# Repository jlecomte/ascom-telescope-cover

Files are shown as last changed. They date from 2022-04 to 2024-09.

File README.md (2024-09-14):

# ASCOM-Compatible Telescope Cover

I do not charge anything to create and maintain these open-source projects. But if you would like to say "thanks" for this project, feel free to send any amount through Paypal using the button below. I appreciate your support!

(https://www.paypal.com/donate/?hosted_button_id=49UXY8F6VVYFA)

:warning: **IMPORTANT:** :warning: This project is no longer actively maintained. Instead, check out [my new Telescope Cover V2](https://github.com/jlecomte/ascom-telescope-cover-v2).

<!-- toc -->

- [Introduction](#introduction)
- [Pre-Requisites](#pre-requisites)
- [Hardware](#hardware)
- [ASCOM Driver](#ascom-driver)
  - [Downloading And Installing The Driver](#downloading-and-installing-the-driver)
  - [Compiling The Driver (For Developers Only)](#compiling-the-driver-for-developers-only)
- [Arduino Firmware](#arduino-firmware)
  - [Microcontroller Compatibility](#microcontroller-compatibility)
  - [Compiling And Uploading The Firmware](#compiling-and-uploading-the-firmware)
- [Mechanical Components](#mechanical-components)
- [Electronic Circuit](#electronic-circuit)
- [Ideas For Future Improvements](#ideas-for-future-improvements)

<!-- tocstop -->

## Introduction

This repository contains code that allows you to build your own automated telescope cover. Here is a short demo video of the finished product, hosted on YouTube. Check it out!

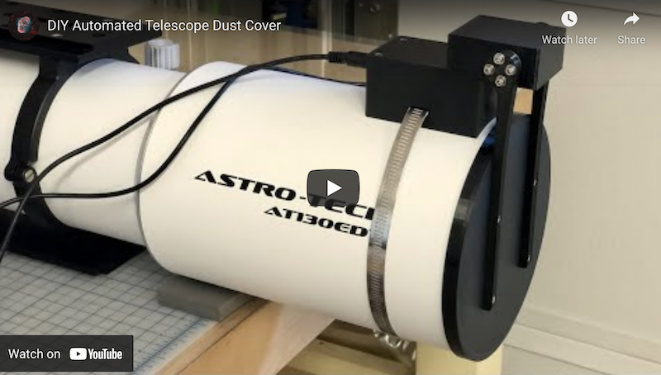
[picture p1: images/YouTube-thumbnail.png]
Short demo video of the finished product (https://www.youtube.com/watch?v=h6WpVCcGNUw)


In this repository, you will find:

* The code for the ASCOM driver (Microsoft Visual Studio 2022 project)
* The code for the Arduino firmware
* The various STL files to 3D print all the mechanical parts
* A blueprint for the electronic circuit

## Pre-Requisites

* A Windows computer (Windows 10 or newer)
* [Microsoft Visual Studio](https://visualstudio.microsoft.com/) (FYI, I used the 2022 edition...)
* [ASCOM Platform](https://ascom-standards.org/)
* [ASCOM Platform Developer Components](https://ascom-standards.org/COMDeveloper/Index.htm)
* [Arduino IDE](https://www.arduino.cc/en/software)
* [FreeCAD](https://www.freecadweb.org/), a free and open-source 3D parametric modeler
* A 3D printer able to print PETG, and a slicer (I use a heavily upgraded Creality Ender 3 v2, and Ultimaker Cura)
* A few basic tools that any tinkerer must own, such as a breadboard, a soldering iron, etc.

## Hardware

The following are just suggestions... Also, over time, some of the Amazon links may no longer work...

* [Seeeduino XIAO](https://www.seeedstudio.com/Seeeduino-XIAO-Arduino-Microcontroller-SAMD21-Cortex-M0+-p-4426.html) (You can get it quicker from Amazon, but you will have to pay twice as much!)
* [Mini360 Buck Converters](https://www.amazon.com/dp/B07T7L51ZW?tag=darkskygeek-20)
* [Perforated Circuit Board (PCB)](https://www.amazon.com/dp/B07NM68FXK?tag=darkskygeek-20)
* [DC Power Jack](https://www.amazon.com/dp/B01N8VV78D?tag=darkskygeek-20)
* [High torque quality Servo with 270° control angle](https://www.amazon.com/dp/B07S9XZYN2?tag=darkskygeek-20)
* [Aluminum Servo Horn](https://www.amazon.com/dp/B07D56FVK5?tag=darkskygeek-20)
* [Bench Power Supply](https://www.amazon.com/dp/B07GCJ5QHF?tag=darkskygeek-20)
* [Threaded inserts for 3D printed parts](https://www.amazon.com/dp/B07VFZWWXY?tag=darkskygeek-20)
* [Assortment of small metric screws, nuts, and washers](https://www.amazon.com/dp/B08JCKH31Q?tag=darkskygeek-20)
* [22AWG solid core electrical wires](https://www.amazon.com/dp/B088KQFHV7?tag=darkskygeek-20)
* [Easy-to-print PETG filament](https://www.amazon.com/dp/B07PGYHYV8?tag=darkskygeek-20)
* [Stainless steel cut-to-length hose clamp](https://www.amazon.com/dp/product/B08Y6LSL3R?tag=darkskygeek-20)

## ASCOM Driver

### Downloading And Installing The Driver

**Step 1:** Download the driver from the [releases page](https://github.com/jlecomte/ascom-telescope-cover/releases), and place the file `ASCOM.DarkSkyGeek.TelescopeCover.dll` somewhere on your system (example: `C:\Users\julien\ascom-telescope-cover\`).

**Step 2:** Open a command prompt, but make sure you run it **as an administrator**!

**Step 3:** Then, proceed with the installation of the driver using `RegAsm.exe`, a utility that should already be present on your system (it comes with the .NET framework). Just don't forget to use the 64 bit version, and to pass the `/tlb /codebase` flags. Here is what it looked like on my imaging mini computer:

```
> cd C:\Users\julien\ascom-telescope-cover\
> C:\Windows\Microsoft.NET\Framework64\v4.0.30319\RegAsm.exe /tlb /codebase ASCOM.DarkSkyGeek.TelescopeCover.dll
Microsoft .NET Framework Assembly Registration Utility version 4.8.4161.0
for Microsoft .NET Framework version 4.8.4161.0
Copyright (C) Microsoft Corporation.  All rights reserved.

Types registered successfully
```

**Note:** The output may be more verbose than the above. As long as it says `Types registered successfully`, you are good to go!

**Note:** During registration, you will see a warning that the assembly is unsigned. This is normal as I did not bother going through the pain of signing the assembly, so you will just have to trust that you are registering the DLL that I built and uploaded to GitHub. And if you don't trust me / GitHub, you can build the DLL yourself using Visual Studio.

**Note:** Once the driver has been installed, make sure you do _not_ delete or move the `ASCOM.DarkSkyGeek.TelescopeCover.dll` file, or things will not work! (if you do move it, you will need to register it again in its new location)

**Step 4:** Start (or restart, if it was already running) N.I.N.A. (or whatever application you use to control your equipment).

### Compiling The Driver (For Developers Only)

Open Microsoft Visual Studio as an administrator (right click on the Microsoft Visual Studio shortcut, and select "Run as administrator") This is required because when building the code, by default, Microsoft Visual Studio will register the necessary COM components, and this operation requires special privileges (Note: This is something you can disable in the project settings...) Then, open the solution (`ASCOM_Driver\ASCOM.DarkSkyGeek.TelescopeCover.sln`), change the solution configuration to `Release` (in the toolbar), open the `Build` menu and click on `Build Solution`. As long as you have properly installed all the required dependencies, the build should succeed and the ASCOM driver will be registered on your system. The binary file generated will be `ASCOM_Driver\bin\Release\ASCOM.DarkSkyGeek.TelescopeCover.dll`. You may also download this file from the [Releases page](https://github.com/jlecomte/ascom-telescope-cover/releases).

## Arduino Firmware

### Microcontroller Compatibility

Pretty much all Arduino-compatible boards should work. There is nothing magical about the firmware. However, see the comment regarding the pins and the servo library. Depending on the exact board you picked, you might have to change that.

### Compiling And Uploading The Firmware

* Add support for Seeeduino boards by following [the instructions from the board manufacturer](https://wiki.seeedstudio.com/Seeeduino-XIAO/).
* To customize the name of the device when connected to your computer, open the file `boards.txt`, which, on my system and for the version of the Seeeduino board I am using, is located at `%LOCALAPPDATA%\Arduino15\packages\Seeeduino\hardware\samd\1.8.2\boards.txt`. Then, change the value of the key `seeed_XIAO_m0.build.usb_product` from `Seeed XIAO M0` (default) to whatever you'd like.
* Finally, connect your Seeeduino board to your computer (make sure you use a USB-C cable that supports data and not just power!), open the sketch file located at `Arduino_Firmware\Arduino_Firmware.ino`, and click on the `Upload` button in the toolbar.

## Mechanical Components

Here is a 3D rendering of all the parts involved in this project:

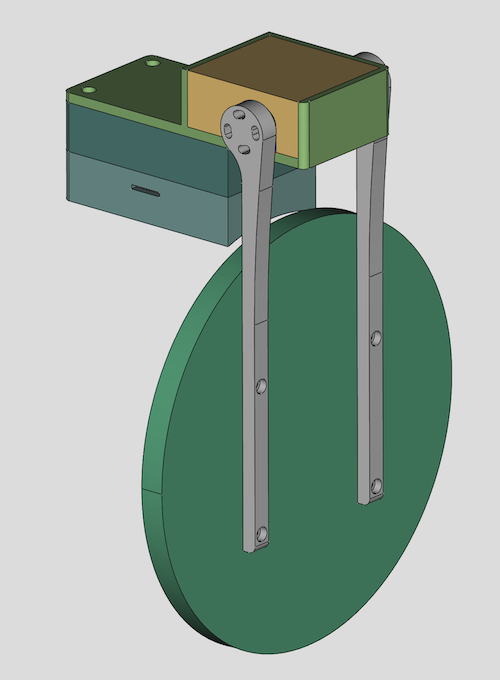
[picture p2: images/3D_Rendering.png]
3D Rendering


The STL files you will find in the `3D_Files/` folder are just a starting point. You will likely have to create your own version of this project, if only to match the base curvature to your own OTA... That is why I included the FreeCAD file in this repository! (also in the `3D_Files/` folder)

## Electronic Circuit

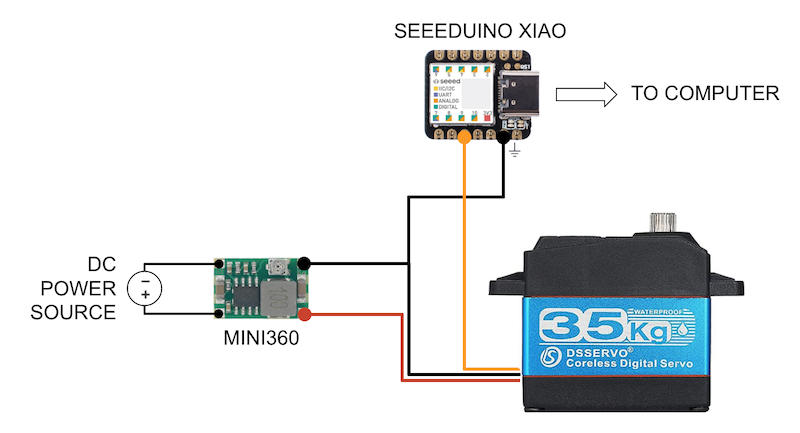
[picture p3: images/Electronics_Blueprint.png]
Electronics Blueprint


Here is what the electronic circuit looks like:

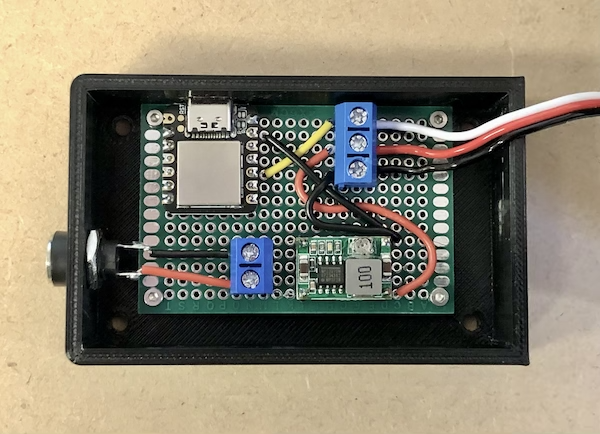
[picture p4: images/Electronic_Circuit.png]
Electronic Circuit


In the photograph above, the components were soldered onto a 60mm x 40mm PCB.

## Ideas For Future Improvements

* Remove the need for a separate 12V power connector, i.e. use the USB cable for both data and power. This change would prevent us from using an Arduino-compatible board because the maximum current that can be delivered by an Arduino-compatible board is usually around 200mA, which is not enough for a powerful servo. In order to do this, you'd have to basically build your own Arduino board using a micro-controller, a USB jack, a USB driver, and many other components... It's quite a project on its own, which is why I decided to go the "easy" route... Alternatively, I found a unit called "PD Micro" which implements USB-C power delivery. I have not tried it yet, but it looks promising.
* Automatically sense the position of the cover before powering up the servo. Right now, if you power up the unit while the cover is open, it will suddenly close very quickly. That can be quite a jarring experience the first time you see it happen. And if something is in the way (example: a flat panel), you could potentially damage your equipment. This could be solved with a simple potentiometer attached to the servo arm.
* Integrate a flat field panel inside the cover. I wanted to keep this project relatively simple, and I did not want to add any more weight to the front end of my already front heavy refractor, so I skipped that, but it can be done and would be a great addition to this project!

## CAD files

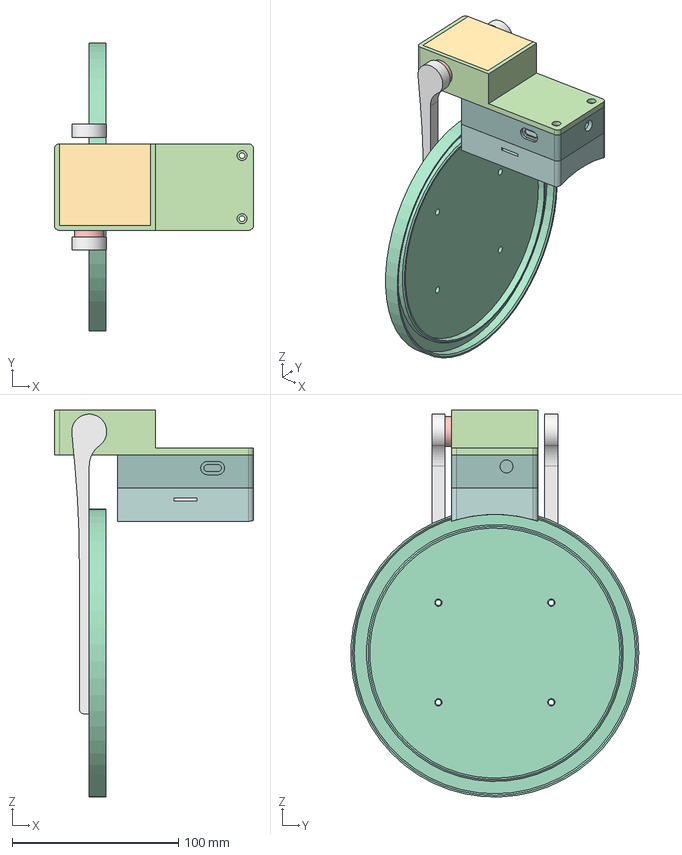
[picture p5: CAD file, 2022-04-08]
3D_Files/Automated-Telescope-Dust-Cover.FCStd
120.0 x 173.2 x 233.0 mm
Circuit Board Box
Base Body
Servo Holder
Servo Lid
Bushing
Cover
Left Cover Arm
Right Cover Arm

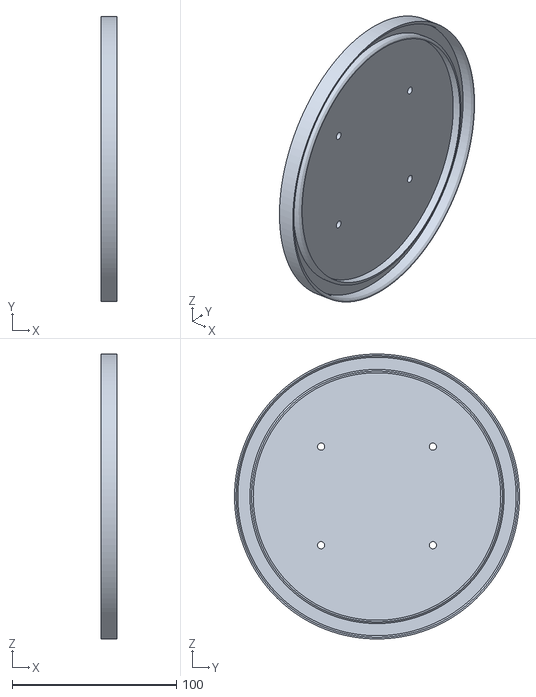
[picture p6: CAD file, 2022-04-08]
3D_Files/Cover.stl
10.0 x 173.4 x 173.3

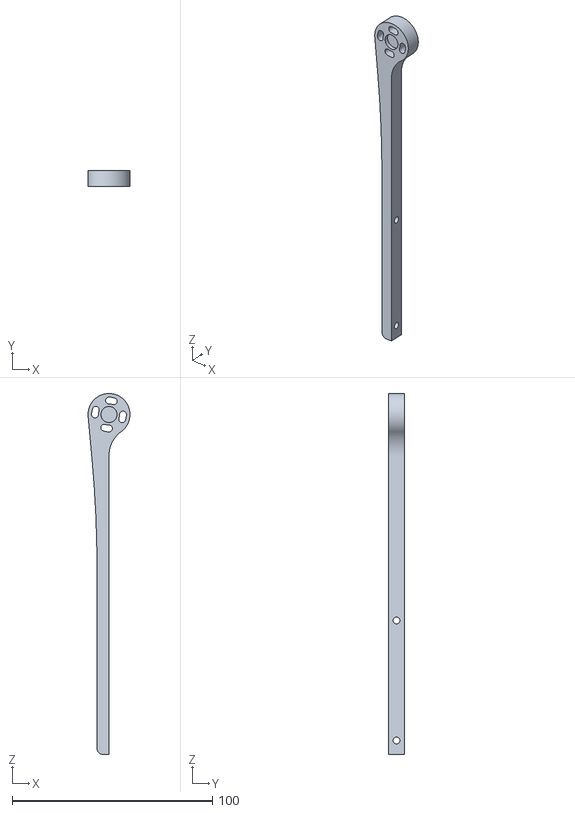
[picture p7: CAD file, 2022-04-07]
3D_Files/Right_Cover_Arm.stl
21.0 x 8.00 x 180.5

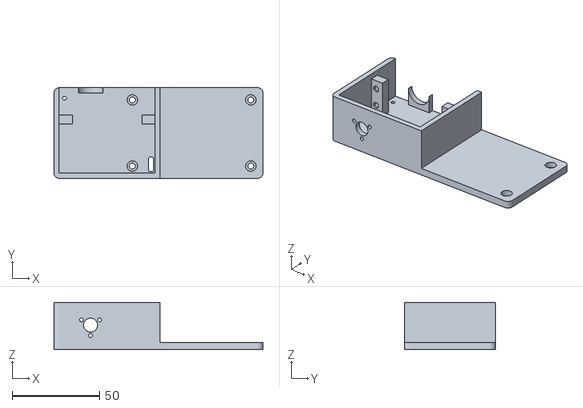
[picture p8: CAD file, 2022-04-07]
3D_Files/Servo_Holder.stl
120.0 x 52.0 x 27.0

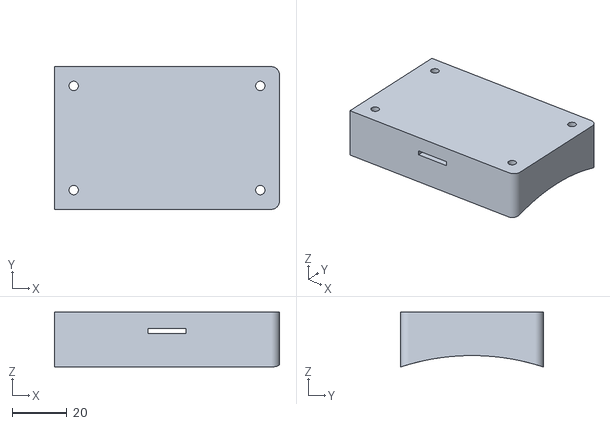
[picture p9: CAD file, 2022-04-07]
3D_Files/Base.stl
82.0 x 52.0 x 20.0

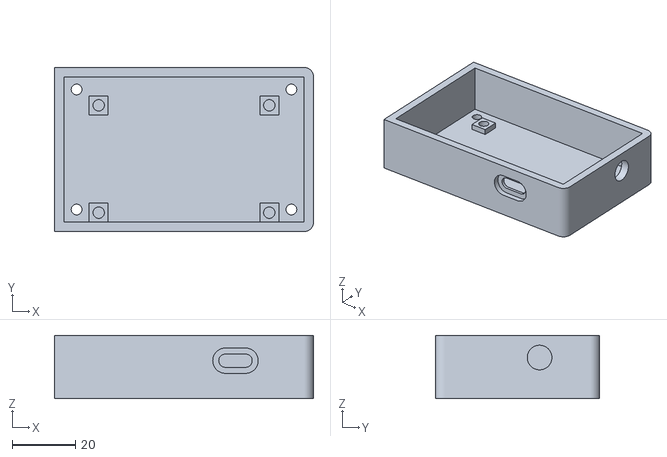
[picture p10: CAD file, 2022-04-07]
3D_Files/Circuit_Board_Box.stl
82.0 x 52.0 x 20.0

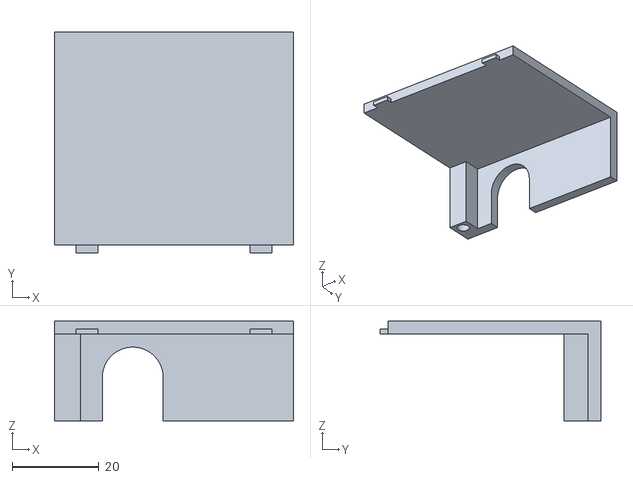
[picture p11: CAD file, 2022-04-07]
3D_Files/Servo_Lid.stl
55.0 x 50.8 x 23.0

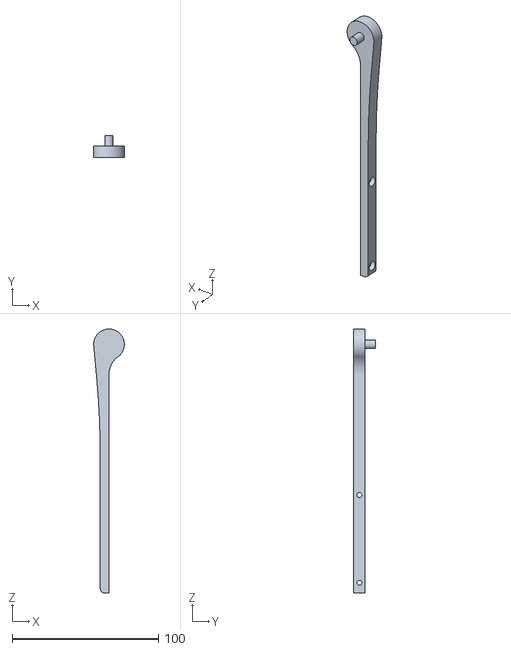
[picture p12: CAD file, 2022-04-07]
3D_Files/Left_Cover_Arm.stl
21.0 x 15.0 x 180.5

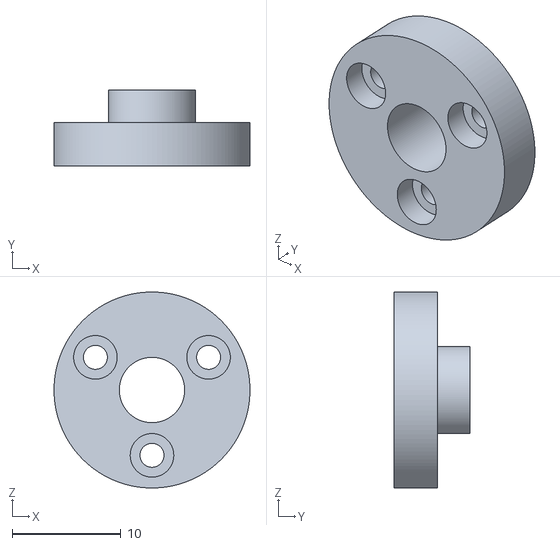
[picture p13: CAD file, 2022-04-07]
3D_Files/Bushing.stl
18.0 x 7.00 x 18.0

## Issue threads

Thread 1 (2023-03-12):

Merge some of your projects

JeffStor, 2023-03-12:
Hello Julien,

No issue, no pull request, just a thought. My name is Jean-Francois, I live in France, and I am a (low level) astrophotographer.
I use NINA and Ascom devices. My setup is EQ6-R / Askar FRA600 /ASI2600color.

I was seeking for an automated dust cap for my telescope and I found your videos ! (Dark Sky Geek)
You did such a great job for 2 projects in which I am interested : dust cap and focuser.
I am not a developer and I discovered your channel today !
I bought hardware stepper-motors drivers called TIC from Pololu and I did a small GUI to drive manually stepper-motors.
This was easy, but to integate TIC with NINA (native or Ascom) is much to dffificult for me.

A stepper-motor and a stepper motor is much less expensive that any Zwo, Pegasus or else equipment.

If for any reason, you plan to use Pololu TIC hardware to drive stepper-motors for your new projects, please let me know.

Sincerely

Jean-Francois
jf.eble@laposte.net

jlecomte, 2023-03-12:
Thank you for your interest. I do not plan to use "Pololu TIC" hardware (I have never heard of that brand before). I generally stick to dirt cheap, standard stepper motors or servos that you can find anywhere online. That being said, adapting what I've done to your specific hardware shouldn't be too difficult. Best of luck!

JeffStor, 2023-03-12:
Thank you for your quick answer. By the way I choosed TIC + stepper-motors because I can buy both on Amazon for around  50 euros (plus a 3D printed hardware for virtually nothing) when a focuser from ZWO or Pegasus costs more than  250 euros

Clear skies !

Closed 2023-03-12.

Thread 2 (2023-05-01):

Issue with FreeCAD model

rlavriv, 2023-05-01:
When I am trying to change globals in FreeCAD model to adjust to my OTA, I get issue with model recompile.

The issue seem to be with USB Connector hole sketch, which shows in a wrong plane:
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

Any ideas how to fix it?

jlecomte, 2023-05-01:
That is because of the topological naming problem, which is a huge issue in FreeCAD. See:

* https://wiki.freecad.org/Topological_naming_problem
*  https://ondsel.com/blog/freecad-topological-naming/

Unfortunately, I did not follow the best practices when designing this model, and therefore it is a victim of this issue.

Since I may upgrade my scope to a larger one, I may completely redesign this in FreeCAD, but this time doing it correctly (and also simplifying the design a bit)...

rlavriv, 2023-05-01:
Is there absolutely no way to salvage it?

jlecomte, 2024-05-25:
I don't think so. Now, I'm hearing that FreeCAD 0.22 will have mostly solved the topological naming issue, so it might be worth trying then. best of luck!

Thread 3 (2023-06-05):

WriteProfile autoDetectComPort alway be true

ZetChang, 2023-06-05:
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

jlecomte, 2023-06-05:
Good catch, thanks!

jlecomte, 2023-06-05:
Fixed in https://github.com/jlecomte/ascom-telescope-cover/commit/37df01e01ec9c3148f8a7f52a69194fa1b1d81bb and release v1.0.1.

ppurbano, 2024-04-14:
Hello. I love their projects and I have made both the flats generator and the telescope cover. I would like to ask you if it would be possible to join the two circuits into a single XIA0. It would be greatly appreciated. A strong greeting

Closed 2023-06-05.

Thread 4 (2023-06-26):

2 servos instead of one ?

aras-vbo, 2023-06-26:
Hello Julien,

Vincent from France. Many thanks for your project ! I'm currently making a cover for my remote telescope.
This is just an idea. Is it possible to control 2 servos from the Xiao at the same time instead of one ? My telescope has a diameter of 250 mm and I'm not able to make a dust cap in just one piece. I need to use 2 parts in shapes of half-circle.
Do you think it could be difficult to add this feature, by changing the Xiao firmware only ?

I think I will try for fun !

Vincent

Closed 2023-06-26.

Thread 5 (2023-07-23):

Not working in NINA

Antiath, 2023-07-23:
NINA doesn't work with your ASCOM driver.  It can connect and open the cover fine. But after asking NINA to open the cover, it times out, preventing me from closing the cover.

I ran the driver along with NINA in Visual Studio to investigate this and I think I know what happens. When lauching the driver, NINA has the switch defaulted to Off and the cover is closed by default of course. All is well for now.  When activating the switch to open the cover, it does so and NINA starts polling the GetSwitchValue method and it expects it to return a 1 when the switch is ON ( i.e cover open). Your driver outputs the opposite. It happens here :

```
     public double GetSwitchValue(short id)
        {
            Validate("GetSwitchValue", id);
            tl.LogMessage("GetSwitchValue", $"GetSwitchValue({id}) - not implemented");
            return QueryDeviceState() ? 1.0 : 0.0;
        }
```
So the solution is simple :
`return QueryDeviceState() ? 0.0 : 1.0;`
and also
` internal static string traceStateDefault = "true"; `

Maybe  a switch driver is not the best option for this application.
Personnaly I would have used a Flatplanel template for the driver, instead of a switch. Even if you don't have an actual flat panel in the cover,  the template provides the methods for the motorised part. So you can just leave the flat side in the code and just implement the motor part.
Also I already have a power box occupying the switch part of NINA, so it's not helpful to have to change driver just to move the cover.

jlecomte, 2023-07-23:
@Antiath I have been using my driver and my device in NINA for well over a year (totaling about 50 nights) and it has worked very reliably.

`QueryDeviceState()` returns `true` if the cover is open, and `false` otherwise, which means that `GetSwitchValue()` will return `1.0` if the cover is open, and `0.0` otherwise. That is the expected behavior.

Antiath, 2023-07-23:
Ah yes my bad, ths issue was with the firmware. I had to modify it a bit to accomodate my servomotor who was weirdly turning the opposite way. And I forgot to check change the state variable accordingly to match this. That is corrected and working as expected now. Case closed.

Nevertheless I will probably reuse the code for and port it to a different driver

Closed 2023-07-23.

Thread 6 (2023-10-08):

Thanks for this project

astroalex80, 2023-10-08:
Dear Julien,

Thanks for making the cover as well as flat panel available.

Converted the cad files to Fusion360 to make them fit my scope. Combined both flat panel and cover functionality.

Honesty my mistake of not having used an SAMD21 / Seeeduino XIAO before. What a powerful tiny piece of electronics.

Instead the usual servo lib I'm using one called slowServo allowing good control of the speed and it is working asynchronously and not blocking when servo moves. It therewith better follows the ASCOM specs like reporting status when moving.

The fact of fast closure move on power-up when cover is not closed I could overcome by writing either panel open, closed or moving to the Flash memory of the XIAO. Therewith current cover status remains on power up, unless the XIAO is disconnected while servo is moving. In this case the cover opens on the re-connection, as feels more save to me before moving fast into the dew shield.

3d parts are printed, cover is moving but wiring is still on a breadboard. Will assemble it next days and happily share some pictures.

Kind regards from Germany,
Alex

jlecomte, 2023-10-09:
Thanks for the kind words, Alex! These are really good suggestions, and I will incorporate some of them into the version 2 of this project, next year. Among other things, I want the cover to know which state it is in when powered up, and this can be accomplished using a potentiometer and a bit of logic in the software. Tschüss!

astroalex80, 2023-10-10:
By the way regarding reading the cover position. I havent been aware they exist but just ordered two of these:
Feetech FB5118M Digital Servo 7.4V 17kg.cm with Position Feedback

There is a 4. wire linked to the internal potentiometer of the servo and therewith having the build-in capability of providing postion.

jlecomte, 2023-10-10:
I did not know that some servos had position feedback. I just ordered one on Amazon, I’ll be experimenting with it. If it works, this would be a brilliant solution! Thanks a lot :)

Closed 2023-10-09.

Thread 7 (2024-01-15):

Control two covers from one computer?

OregonAstronomer, 2024-01-15:
Hi,
First, I'd like to thank you for this great project. It has been working flawlessly in my remote observatory for the past year!
I'm planning on adding a second camera with an attached telephoto lens piggyback on top of the scope I am currently using and would like to also equip it with one of your covers. Is it possible to control two covers using two instances of NINA from a single computer?
Thank you so much for your time.
Sincerely,
Arnie (OregonAstronomer)

Adler6907, 2024-01-15:
I programmed an extension for exactly this.

https://github.com/Adler6907/ascom-telescope-cover/tree/Adler6907-multiple-Telescope-Cover

jlecomte, 2024-01-15:
Yes, it is possible to control two covers using two instances of NINA on a single computer.

OregonAstronomer, 2024-01-16:
Thank you both so much!

Closed 2024-01-15.

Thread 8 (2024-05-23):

Added control (third state) to turn on flatpanel (and added COMMAND:FLAT in ARDUINO project), but...

thegoodpope, 2024-05-23:
...but i cannot regasm the assembly.

My Visual Studio 2019 refuses to install as COM the resulting dll.
"RA0000 .... is not a valid assembly."
I'm a programmer but not expert with C# and Visual studio in general. Is there something I've to change in order to compile and install the driver?
I ask to you because:
1) I cannot find real and useful explanations. I've attempted to put signature, change GUID and a lot of other things
2) I cannot install - also - the compiled result of your original code
3) nevertheless the installation of your COM dll component (very useful your HUB also! Thank you) runs perfectly...so are there differences between the COM component you distribute and the project you share?

Thanks in every case for your project. I've customized the original cap/legs/base for my scope (a 20cm newton) and all went well.

jlecomte, 2024-05-24:
> Is there something I've to change in order to compile and install the driver?

No. It should work out of the box. This, however, assumes that you already have the ASCOM platform installed on your development computer.

Closed 2024-05-24.

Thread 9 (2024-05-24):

Cannot connect properly in NINA

sidiouss, 2024-05-24:
Hello,
I've successfully prepared slightly modified flat panel and telescope cover projects which I am very thankful for. I managed to register both drivers and setup properly the flat panel in Nina. However, I cannot launch the cover in the Nina software. It says both that the switch is connected, but then also prompts that there is invalid response from the cover. Can you help me investigating this issue?
The cover properly shows up in the device manager as a com port, I can send the commands through the COM terminal so I know the cover works, but I cannot launch it with NINA. I am using the newest dll and firmware is uploaded to Arduino Nano.

Prompt from NINA:
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

jlecomte, 2024-05-24:
I do not know what is causing this, and I cannot provide you with any support.

sidiouss, 2024-05-25:
Hi,
You may not be eager to solve such problems and I understand that. However, I have run conformance checker on your driver and as you are more familiar with ASCOM platform, maybe you could identify the underlying issue presented in the following report:

ConformanceCheck ASCOM Device Conformance Checker Version 6.6.8048.17861, Build time: 2022-01-13 08:55:24
ConformanceCheck Running on: ASCOM Platform 6.6 SP2 6.6.2.4294

ConformanceCheck Driver ProgID: ASCOM.DarkSkyGeek.Switch

Error handling
Error number for "Not Implemented" is: 80040400
Error number for "Invalid Value 1" is: 80040405
Error number for "Value Not Set 1" is: 80040402
Error number for "Value Not Set 2" is: 80040403
Error messages will not be interpreted to infer state.

21:45:03.873 Driver Access Checks              OK
21:45:04.535 AccessChecks                      OK       Successfully created driver using late binding
21:45:06.583 AccessChecks                      OK       Successfully connected using late binding
21:45:06.588 AccessChecks                      INFO     The driver is a .NET object
21:45:06.593 AccessChecks                      INFO     The AssemblyQualifiedName is: ASCOM.DarkSkyGeek.Switch, ASCOM.DarkSkyGeek.TelescopeCover, Version=1.0.0.0,
21:45:06.599 AccessChecks                      INFO     The driver implements interface: ASCOM.DeviceInterface.ISwitchV2
21:45:07.277 AccessChecks                      INFO     Device does not expose interface ISwitch
21:45:09.339 AccessChecks                      INFO     Device exposes interface ISwitchV2
21:45:10.014 AccessChecks                      OK       Successfully created driver using driver access toolkit
21:45:12.063 AccessChecks                      OK       Successfully connected using driver access toolkit

Conform is using ASCOM.DriverAccess.Switch to get a Switch object
21:45:12.099 ConformanceCheck                  OK       Driver instance created successfully
21:45:14.211 ConformanceCheck                  OK       Connected OK

Common Driver Methods
21:45:14.265 InterfaceVersion                  OK       2
21:45:14.305 Connected                         OK       True
21:45:14.352 Description                       OK       DarkSkyGeek’s Telescope Cover
21:45:14.398 DriverInfo                        OK       DarkSkyGeek’s Telescope Cover ASCOM Driver Version 1.0
21:45:14.445 DriverVersion                     OK       1.0
21:45:14.492 Name                              OK       DarkSkyGeek’s Telescope Cover
21:45:14.538 CommandString                     INFO     Conform cannot test the CommandString method
21:45:14.547 CommandBlind                      INFO     Conform cannot test the CommandBlind method
21:45:14.557 CommandBool                       INFO     Conform cannot test the CommandBool method
21:45:14.565 Action                            INFO     Conform cannot test the Action method
21:45:14.574 SupportedActions                  OK       Driver returned an empty action list

Properties
21:45:14.734 MaxSwitch                         OK       1

Methods
21:45:15.001 SwitchNumber                      ISSUE    Received ASCOM.DriverException(0x80040401), please use ASCOM.InvalidValueException to report invalid values
21:45:15.009 SwitchNumber                      ERROR    Unexpected DriverException(0x80040401), when a switch ID below 0 was used in method: CanWrite: CanWrite set - '-1' is an invalid value. The valid range is: 0 to 0.
21:45:15.019 SwitchNumber                      ISSUE    Received ASCOM.DriverException(0x80040401), please use ASCOM.InvalidValueException to report invalid values
21:45:15.027 SwitchNumber                      ERROR    Unexpected DriverException(0x80040401), when a switch ID above MaxSwitch was used in method: CanWrite: CanWrite set - '2' is an invalid value. The valid range is: 0 to 0.
21:45:15.037 SwitchNumber                      ISSUE    Received ASCOM.DriverException(0x80040401), please use ASCOM.InvalidValueException to report invalid values
21:45:15.045 SwitchNumber                      ERROR    Unexpected DriverException(0x80040401), when a switch ID below 0 was used in method: GetSwitch: GetSwitch set - '-1' is an invalid value. The valid range is: 0 to 0.
21:45:15.055 SwitchNumber                      ISSUE    Received ASCOM.DriverException(0x80040401), please use ASCOM.InvalidValueException to report invalid values
21:45:15.063 SwitchNumber                      ERROR    Unexpected DriverException(0x80040401), when a switch ID above MaxSwitch was used in method: GetSwitch: GetSwitch set - '2' is an invalid value. The valid range is: 0 to 0.
21:45:15.075 SwitchNumber                      ISSUE    Received ASCOM.DriverException(0x80040401), please use ASCOM.InvalidValueException to report invalid values
21:45:15.085 SwitchNumber                      ERROR    Unexpected DriverException(0x80040401), when a switch ID below 0 was used in method: GetSwitchDescription: GetSwitchDescription set - '-1' is an invalid value. The valid range is: 0 to 0.
21:45:15.095 SwitchNumber                      ISSUE    Received ASCOM.DriverException(0x80040401), please use ASCOM.InvalidValueException to report invalid values
21:45:15.106 SwitchNumber                      ERROR    Unexpected DriverException(0x80040401), when a switch ID above MaxSwitch was used in method: GetSwitchDescription: GetSwitchDescription set - '2' is an invalid value. The valid range is: 0 to 0.
21:45:15.119 SwitchNumber                      ISSUE    Received ASCOM.DriverException(0x80040401), please use ASCOM.InvalidValueException to report invalid values
21:45:15.126 SwitchNumber                      ERROR    Unexpected DriverException(0x80040401), when a switch ID below 0 was used in method: GetSwitchName: GetSwitchName set - '-1' is an invalid value. The valid range is: 0 to 0.
21:45:15.138 SwitchNumber                      ISSUE    Received ASCOM.DriverException(0x80040401), please use ASCOM.InvalidValueException to report invalid values
21:45:15.147 SwitchNumber                      ERROR    Unexpected DriverException(0x80040401), when a switch ID above MaxSwitch was used in method: GetSwitchName: GetSwitchName set - '2' is an invalid value. The valid range is: 0 to 0.
21:45:15.158 SwitchNumber                      ISSUE    Received ASCOM.DriverException(0x80040401), please use ASCOM.InvalidValueException to report invalid values
21:45:15.168 SwitchNumber                      ERROR    Unexpected DriverException(0x80040401), when a switch ID below 0 was used in method: GetSwitchValue: GetSwitchValue set - '-1' is an invalid value. The valid range is: 0 to 0.
21:45:15.178 SwitchNumber                      ISSUE    Received ASCOM.DriverException(0x80040401), please use ASCOM.InvalidValueException to report invalid values
21:45:15.188 SwitchNumber                      ERROR    Unexpected DriverException(0x80040401), when a switch ID above MaxSwitch was used in method: GetSwitchValue: GetSwitchValue set - '2' is an invalid value. The valid range is: 0 to 0.
21:45:15.200 SwitchNumber                      ISSUE    Received ASCOM.DriverException(0x80040401), please use ASCOM.InvalidValueException to report invalid values
21:45:15.209 SwitchNumber                      ERROR    Unexpected DriverException(0x80040401), when a switch ID below 0 was used in method: MaxSwitchValue: MaxSwitchValue set - '-1' is an invalid value. The valid range is: 0 to 0.
21:45:15.221 SwitchNumber                      ISSUE    Received ASCOM.DriverException(0x80040401), please use ASCOM.InvalidValueException to report invalid values
21:45:15.229 SwitchNumber                      ERROR    Unexpected DriverException(0x80040401), when a switch ID above MaxSwitch was used in method: MaxSwitchValue: MaxSwitchValue set - '2' is an invalid value. The valid range is: 0 to 0.
21:45:15.241 SwitchNumber                      ISSUE    Received ASCOM.DriverException(0x80040401), please use ASCOM.InvalidValueException to report invalid values
21:45:15.258 SwitchNumber                      ERROR    Unexpected DriverException(0x80040401), when a switch ID below 0 was used in method: MinSwitchValue: MinSwitchValue set - '-1' is an invalid value. The valid range is: 0 to 0.
21:45:15.270 SwitchNumber                      ISSUE    Received ASCOM.DriverException(0x80040401), please use ASCOM.InvalidValueException to report invalid values
21:45:15.281 SwitchNumber                      ERROR    Unexpected DriverException(0x80040401), when a switch ID above MaxSwitch was used in method: MinSwitchValue: MinSwitchValue set - '2' is an invalid value. The valid range is: 0 to 0.
21:45:15.294 SwitchNumber                      ISSUE    Received ASCOM.DriverException(0x80040401), please use ASCOM.InvalidValueException to report invalid values
21:45:15.305 SwitchNumber                      ERROR    Unexpected DriverException(0x80040401), when a switch ID below 0 was used in method: SetSwitch: SetSwitch set - '-1' is an invalid value. The valid range is: 0 to 0.
21:45:15.320 SwitchNumber                      ISSUE    Received ASCOM.DriverException(0x80040401), please use ASCOM.InvalidValueException to report invalid values
21:45:15.330 SwitchNumber                      ERROR    Unexpected DriverException(0x80040401), when a switch ID above MaxSwitch was used in method: SetSwitch: SetSwitchValue set - '2' is an invalid value. The valid range is: 0 to 0.
21:45:15.343 SwitchNumber                      ISSUE    Received ASCOM.DriverException(0x80040401), please use ASCOM.InvalidValueException to report invalid values
21:45:15.356 SwitchNumber                      ERROR    Unexpected DriverException(0x80040401), when a switch ID below 0 was used in method: SetSwitchValue: SetSwitchValue set - '-1' is an invalid value. The valid range is: 0 to 0.
21:45:15.369 SwitchNumber                      ISSUE    Received ASCOM.DriverException(0x80040401), please use ASCOM.InvalidValueException to report invalid values
21:45:15.379 SwitchNumber                      ERROR    Unexpected DriverException(0x80040401), when a switch ID above MaxSwitch was used in method: SetSwitchValue: SetSwitchValue set - '2' is an invalid value. The valid range is: 0 to 0.
21:45:15.394 SwitchNumber                      ISSUE    Received ASCOM.DriverException(0x80040401), please use ASCOM.InvalidValueException to report invalid values
21:45:15.406 SwitchNumber                      ERROR    Unexpected DriverException(0x80040401), when a switch ID below 0 was used in method: SwitchStep: SwitchStep set - '-1' is an invalid value. The valid range is: 0 to 0.
21:45:15.419 SwitchNumber                      ISSUE    Received ASCOM.DriverException(0x80040401), please use ASCOM.InvalidValueException to report invalid values
21:45:15.430 SwitchNumber                      ERROR    Unexpected DriverException(0x80040401), when a switch ID above MaxSwitch was used in method: SwitchStep: SwitchStep set - '2' is an invalid value. The valid range is: 0 to 0.
21:45:18.735 GetSwitchName                     OK       Found switch 0
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

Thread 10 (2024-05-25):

Problems in WIN11 64bit

thegoodpope, 2024-05-25:
This terrific complexity with Window versions, 32/64 bit, ASCOM versions, .NET frameworks will kill me...
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

thegoodpope, 2024-05-25:
Registering in 32 bit ascom is ok, but when I tyy to connect in NINA
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

jlecomte, 2024-05-25:
I have had no such problem. I'm not sure what you're doing, but the Visual Studio project should be configured properly out of the box. When I last published the DLL, I simply opened the project, built it, and copied the DLL.

thegoodpope, 2024-05-26:
I've done the same, but got problems with regasm as i've alteady written.
This last thing has not to do with recompilation: I used your original
compiled DLL as downloaded from the resources sectiin. In my old PC It
worked flawlessy, buy when i've tried to install It on the win11 PC that
controls mount and camera (remotely) It has occurred the strange
situation....

Il dom 26 mag 2024, 01:51 Julien Lecomte ***@***.***> ha
scritto:

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

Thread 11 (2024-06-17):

Adjusting servo end courses and speed (delay)

vef445, 2024-06-17:
Hi,
First of all, be aware that I'm in no way a professional developer :)

With the driver you built, I wasn't able to get the full course of my 270deg. servo. A quick investigation revealed that the default values provided by Servo.h when attaching the servo (min pulse width = 544 and max pulse width = 2400) were not ideal for my setup. (Using the cheap servos from Amazon that you listed).

Instead of just editing the Arduino code with alternative (and fixed) values, I decided to add 'pulse min' and 'pulse max' as part of the Ascom driver profile.
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
While I was there, I also added the servo write "delay" as a parameter too. (the default value 30 isn't the best for my setup).

The three parameters are sent to the Arduino upon connection of the device in Nina. Please check how it's parsed on the Arduino side; it's a little dirty... (but it works :) )

I have no idea how I can properly share my code with you or if you're even interested. I'm simply attaching a ZIP below that contains both the driver and the Arduino file. Let me know if there is a better method.
[Motorized_cover_guillaume.zip](https://github.com/user-attachments/files/15865544/Motorized_cover_guillaume.zip)

Comments/critics very welcome!

-Guillaume

PS: Awesome job you did there! I already built two motorized covers, including one for my C11 and, despite the large size, it works perfectly.

jlecomte, 2024-06-17:
Hello! Great work! Note that this project is now on life support so I will not make any changes to it. However, I have been working on a new version of this project, which brings a lot of improvements, and fixes the servo pulse min/max thing you mentioned. I do not have an ETA to release that project. Thanks!

vef445, 2024-06-17:
> Hello! Great work! Note that this project is now on life support so I will not make any changes to it. However, I have been working on a new version of this project, which brings a lot of improvements, and fixes the servo pulse min/max thing you mentioned. I do not have an ETA to release that project. Thanks!

I’ll keep an eye on what’s coming next!

Closed 2024-06-17.

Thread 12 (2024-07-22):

servo motor experiences jolts

jduffas, 2024-07-22:
Hello,

I have installed your "Ascom Telescope Cover" which works perfectly with N.I.N.A. However, I am facing a small problem: from time to time, and quite often, the servo motor experiences jolts, causing vibrations in the telescope, resulting in blurred images (I do astrophotography).

The solution I found is to cut the 12V power supply with a switch controlled by Arduino (and therefore by N.I.N.A.), but there is an issue. Indeed, when the servo motor is no longer powered, the cover is not held in place, which can unbalance the telescope when it moves.

Do you have any idea how to limit or completely eliminate these vibrations from the servo motor?

Thank you in advance for your help.

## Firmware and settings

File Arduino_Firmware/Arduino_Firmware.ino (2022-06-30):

/*
 * Arduino_Firmware.ino
 * Copyright (C) 2022 - Present, Julien Lecomte - All Rights Reserved
 * Licensed under the MIT License. See the accompanying LICENSE file for terms.
 */

#include <Servo.h>

constexpr auto DEVICE_GUID = "b45ba2c9-f554-4b4e-a43c-10605ca3b84d";

constexpr auto COMMAND_PING = "COMMAND:PING";
constexpr auto RESULT_PING = "RESULT:PING:OK:";

constexpr auto COMMAND_INFO = "COMMAND:INFO";
constexpr auto RESULT_INFO = "RESULT:DarkSkyGeek's Telescope Cover Firmware v1.0";

constexpr auto COMMAND_GETSTATE = "COMMAND:GETSTATE";
constexpr auto RESULT_STATE_UNKNOWN = "RESULT:STATE:UNKNOWN";
constexpr auto RESULT_STATE_OPEN = "RESULT:STATE:OPEN";
constexpr auto RESULT_STATE_CLOSED = "RESULT:STATE:CLOSED";

constexpr auto COMMAND_OPEN = "COMMAND:OPEN";
constexpr auto COMMAND_CLOSE = "COMMAND:CLOSE";

constexpr auto ERROR_INVALID_COMMAND = "ERROR:INVALID_COMMAND";

enum CoverState {
    open,
    closed
} state;

Servo servo;

// The `setup` function runs once when you press reset or power the board.
void setup() {
    state = closed;

    // Initialize serial port I/O.
    Serial.begin(57600);
    while (!Serial) {
        ; // Wait for serial port to connect. Required for native USB!
    }
    Serial.flush();

    // Initialize servo.
    // Important: We assume that the cover is in the closed position!
    // If it's not, then the servo will brutally close it when the system is powered up!
    // That may damage the mechanical parts, so be careful...
    servo.write(0);
    servo.attach(9);

    // Make sure the RX, TX, and built-in LEDs don't turn on, they are very bright!
    // Even though the board is inside an enclosure, the light can be seen shining
    // through the small opening for the USB connector! Unfortunately, it is not
    // possible to turn off the power LED (green) in code...
    pinMode(PIN_LED_TXL, INPUT);
    pinMode(PIN_LED_RXL, INPUT);
    pinMode(LED_BUILTIN, OUTPUT);
    digitalWrite(LED_BUILTIN, HIGH);
}

// The `loop` function runs over and over again until power down or reset.
void loop() {
    if (Serial.available() > 0) {
        String command = Serial.readStringUntil('\n');
        if (command == COMMAND_PING) {
            handlePing();
        }
        else if (command == COMMAND_INFO) {
            sendFirmwareInfo();
        }
        else if (command == COMMAND_GETSTATE) {
            sendCurrentState();
        }
        else if (command == COMMAND_OPEN) {
            openCover();
        }
        else if (command == COMMAND_CLOSE) {
            closeCover();
        }
        else {
            handleInvalidCommand();
        }
    }
}

void handlePing() {
    Serial.print(RESULT_PING);
    Serial.println(DEVICE_GUID);
}

void sendFirmwareInfo() {
    Serial.println(RESULT_INFO);
}

void sendCurrentState() {
    switch (state) {
    case open:
        Serial.println(RESULT_STATE_OPEN);
        break;
    case closed:
        Serial.println(RESULT_STATE_CLOSED);
        break;
    default:
        Serial.println(RESULT_STATE_UNKNOWN);
        break;
    }
}

void openCover() {
    int pos = servo.read();
    // Serial.print("Current position of servo is ");
    // Serial.println(pos);
    if (pos < 180) {
        for (; pos <= 180; pos++) {
            servo.write(pos);
            delay(30);
        }
    }

    state = open;
}

void closeCover() {
    int pos = servo.read();
    // Serial.print("Current position of servo is ");
    // Serial.println(pos);
    if (pos > 0) {
        for (; pos >= 0; pos--) {
            servo.write(pos);
            delay(30);
        }
    }

    state = closed;
}

void handleInvalidCommand() {
    Serial.println(ERROR_INVALID_COMMAND);
}

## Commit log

2022-04-07 Added STL files
    [Base.stl, Bushing.stl, Circuit_Board_Box.stl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]
2022-04-07 Added FreeCAD file and images
    [Automated-Telescope-Dust-Cover.FCStd, Base.stl, Bushing.stl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]
2022-04-08 Updated CAD model and README
    [Automated-Telescope-Dust-Cover.FCStd, Cover.stl]
2022-04-08 Minor tweaks to the cover
    [Automated-Telescope-Dust-Cover.FCStd, Cover.stl]
2022-04-24 Added details about registration of ASCOM driver
2022-06-30 Turn off all LEDs on Xiao board
2022-11-30 Removed driver template file
